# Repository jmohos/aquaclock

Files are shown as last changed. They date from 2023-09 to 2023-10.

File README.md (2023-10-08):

# AquaClock

## **What is this thing?**

The AquaClock project is a kinetic clock using water, tubes, ESP32, pumps, valves, time-of-flight sensors and Arduino to display time.

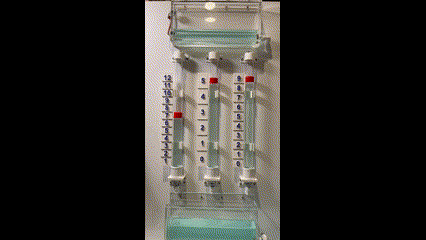
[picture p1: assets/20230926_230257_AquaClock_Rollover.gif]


## Why?

I love clocks.  The more unique the better.  One day I was touring the Queen Mary engine room and I fell in love with the steampunk style gauges.  Then inspiration hit me, why not make a clock that quietly tells time using a floating marker?

After 4 months of tinkering on Fusion360, printing 30+ 3D parts, building Arduino SW, ordering parts from Amazon, DigiKey and Pololu I have a working prototype!

## Design Goals

* Has to tell time in the form of Hours and Minutes.
* Has to be silent.  Only a slight purring of a quiet pump once an hour max.
* Has to show organic movement.
* Has to be wall hangable to install in my office.
* Has to be accurate and battery backed.
* Has to run without the need for Wifi or bluetooth.
* Has to support sleeping during specified hours.
* Has to be readable from across my office from a wide viewing angle.
* Has to have a simple user interface to set the time, set sleep periods and calibrate the markers.
* Has to manage transfering water between tanks fully automated.
* Has to be captured in a CAD program to share with others.
* Has to be fun to watch!

## 3D Design on Fusion 360

One of my personal goals was to capture the design in a 3D CAD program.  I have been playing with Fusion 360 and really enjoy using it.  So I started to pull together acrylic tubes, 1/4" tubing, fittings and colored water to experiment with gravity fed water regulation.

The result is dozens of components comprised of off the shelf parts and custom parts.  I wanted to highlight not just the water in the tubes to tell time but also the tanks holding the water for gravity feeding.  The clock needs to be kinetic, moving and organic.

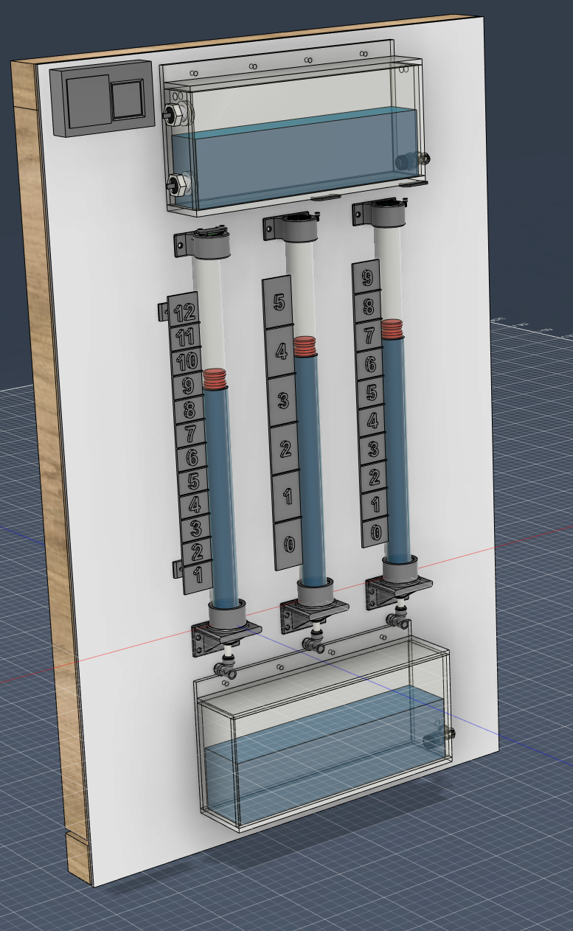
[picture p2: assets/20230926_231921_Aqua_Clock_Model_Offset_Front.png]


The back shows the array of valves, pump, plumbing and electronics to make it al work together.

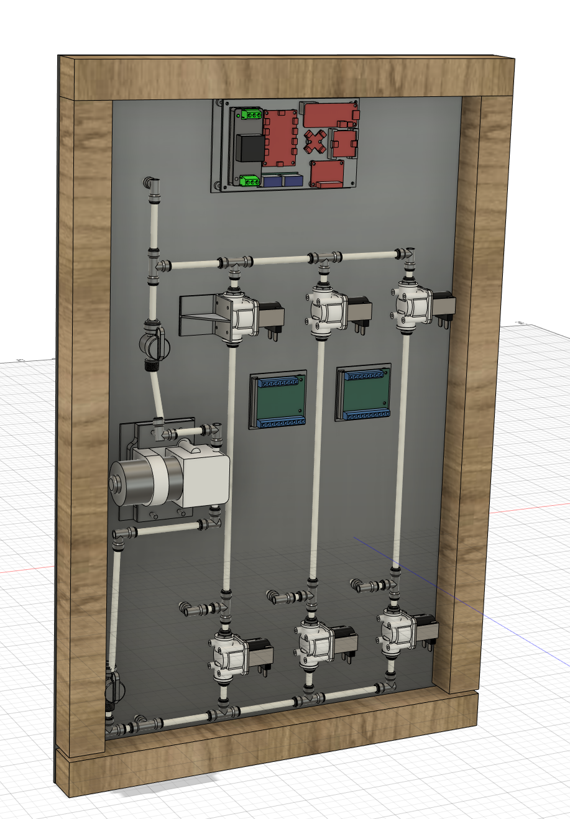
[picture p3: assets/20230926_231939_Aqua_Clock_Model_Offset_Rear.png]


## The Results

After 3D printing, fitting, glueing, sanding, painting, soldiering, criming and fastening this is the result:

Front View:



Rear View:



Here are the details highlighted:





## The Electronics
Architecture:
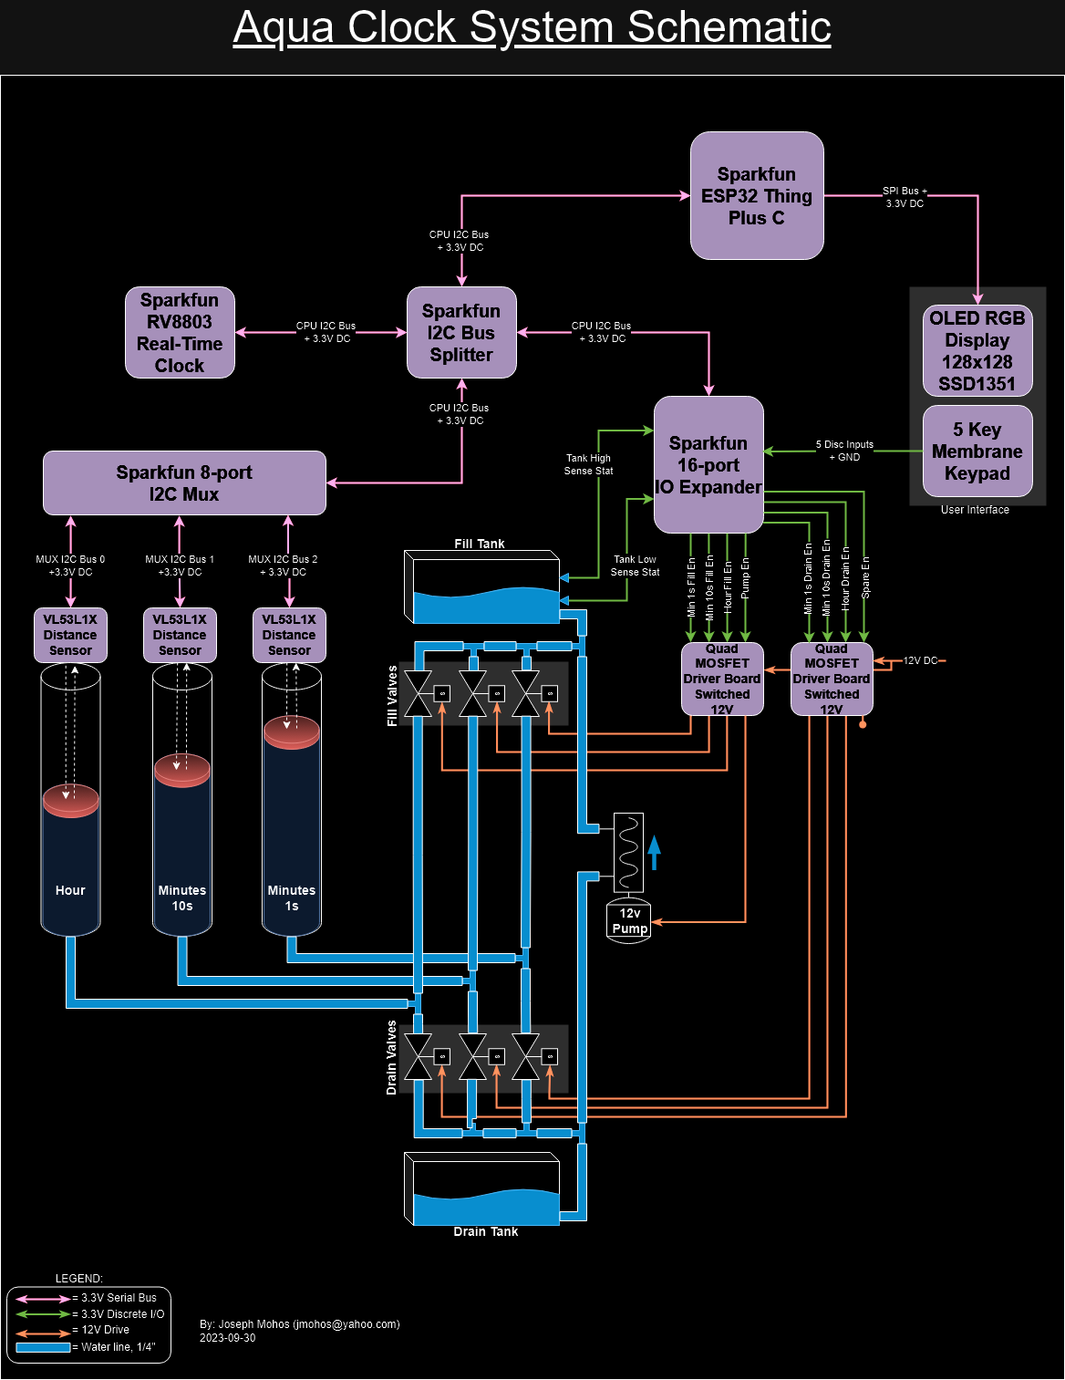
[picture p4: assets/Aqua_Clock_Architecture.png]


Schematics:
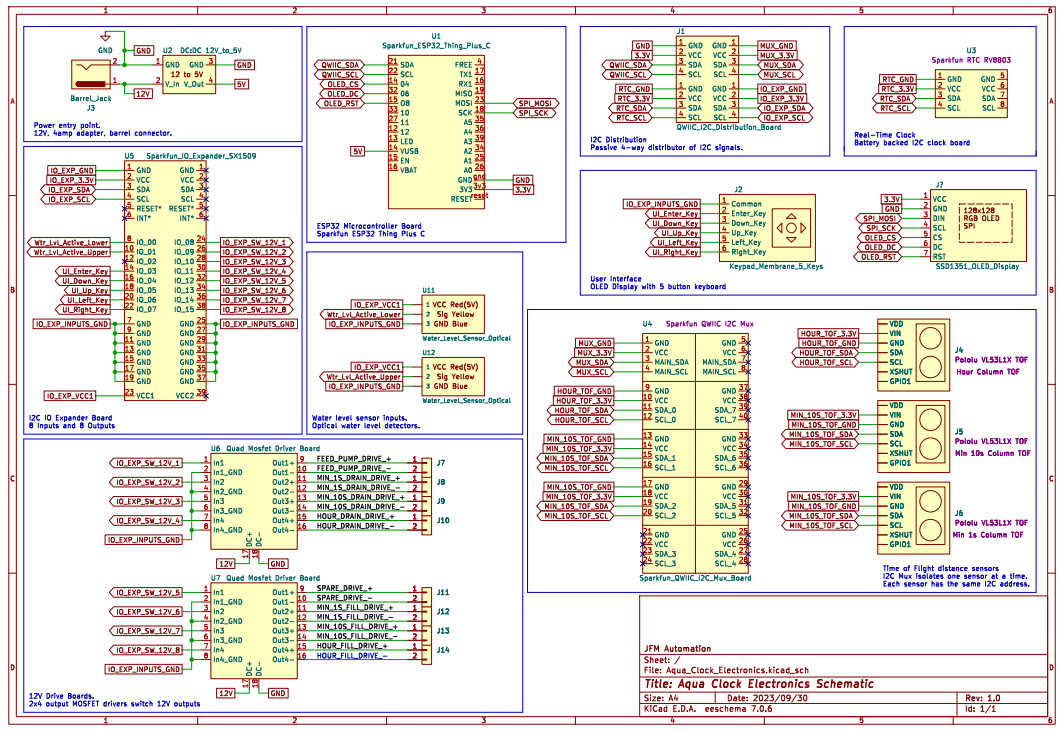
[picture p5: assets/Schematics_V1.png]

## The Software

The Sparkfun ESP32 Thing Plus C is the heart of the controls assembly.

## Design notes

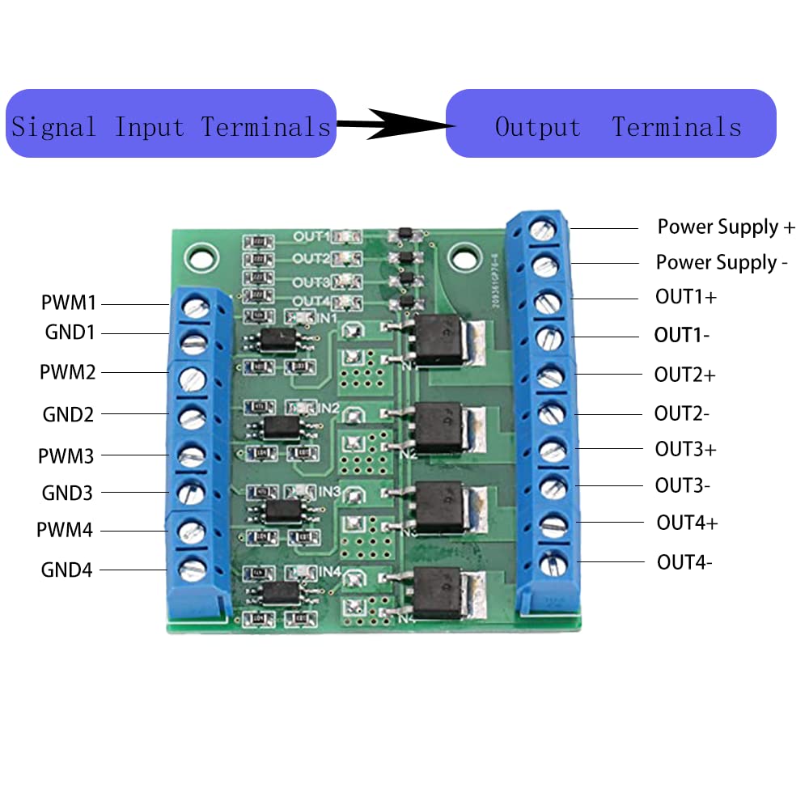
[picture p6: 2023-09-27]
parts/Quad_MOSFET_Driver_Board/Quad_Driver_Board_Pinout.jpg

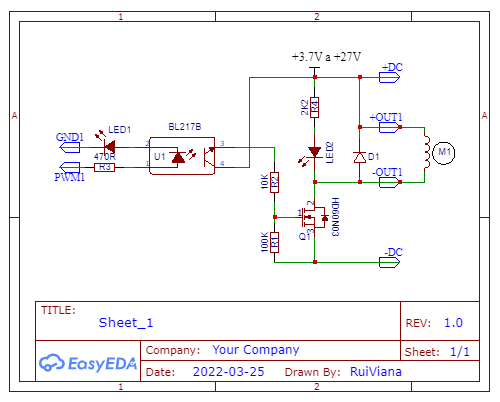
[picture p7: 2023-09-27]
parts/Quad_MOSFET_Driver_Board/Rough_Schematic.png

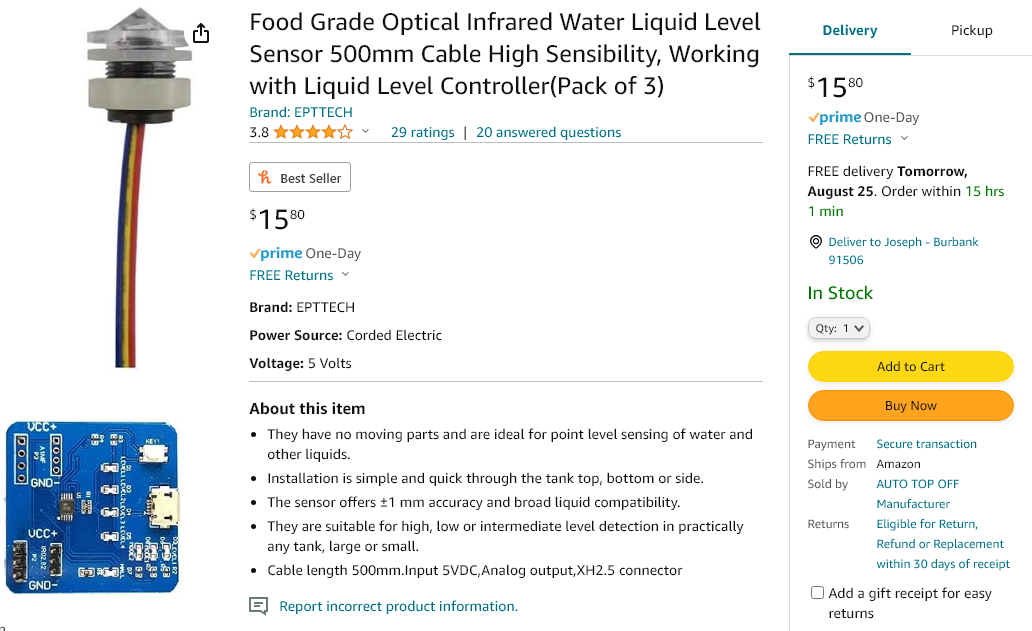
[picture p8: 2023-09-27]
parts/Water_Level_Sensor_-_Optical/Amazon_Listing.png

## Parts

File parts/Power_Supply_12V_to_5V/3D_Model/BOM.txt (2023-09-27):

3DX_CUI_Supplier: CUI, Inc
3DX_CUI_Description: 5 Vdc, 2 A, 10 W, 9~36 Vdc Input Range
3DX_CUI_Model Number: PDQE10-Q24-S5-T

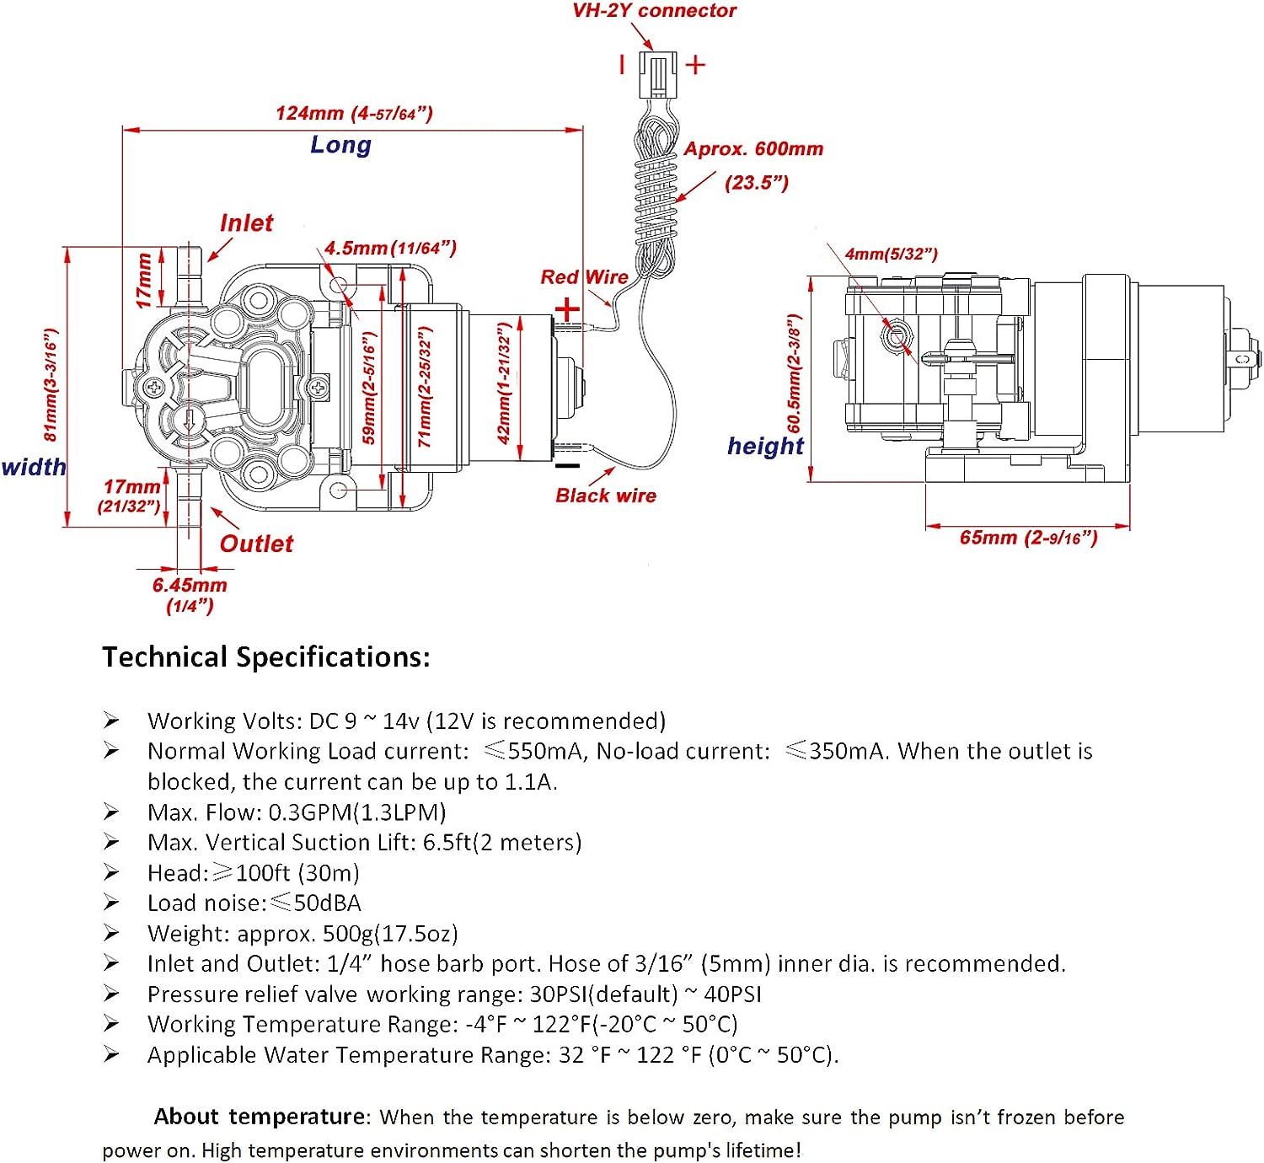
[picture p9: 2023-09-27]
parts/Water_Pump_12V/715-BqpBXsL._AC_SL1500_.jpg

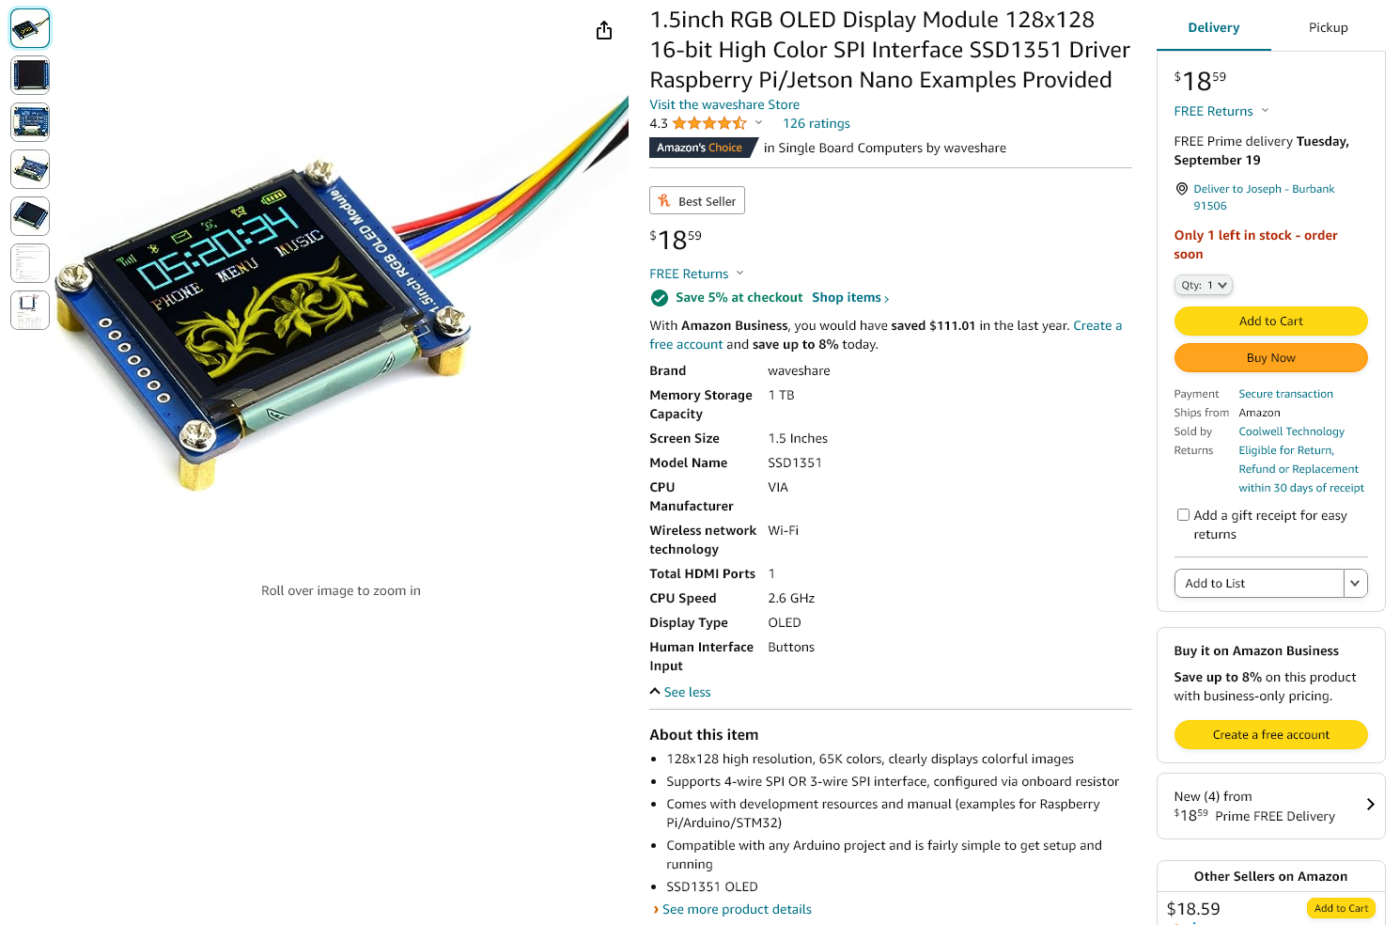
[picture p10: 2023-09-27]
parts/OLED_Display_1_5inch_Waveshare_SSD1351_128x128/Amazon_Part.png

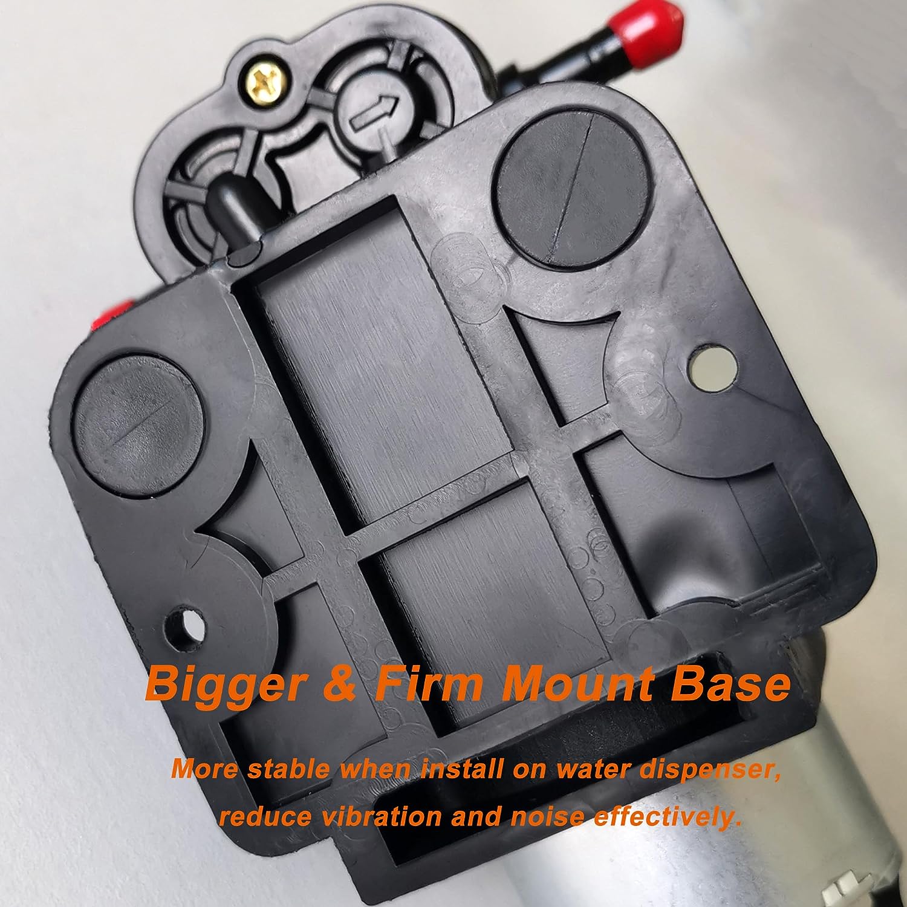
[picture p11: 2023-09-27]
parts/Water_Pump_12V/817y4+fEQSL._AC_SL1500_.jpg

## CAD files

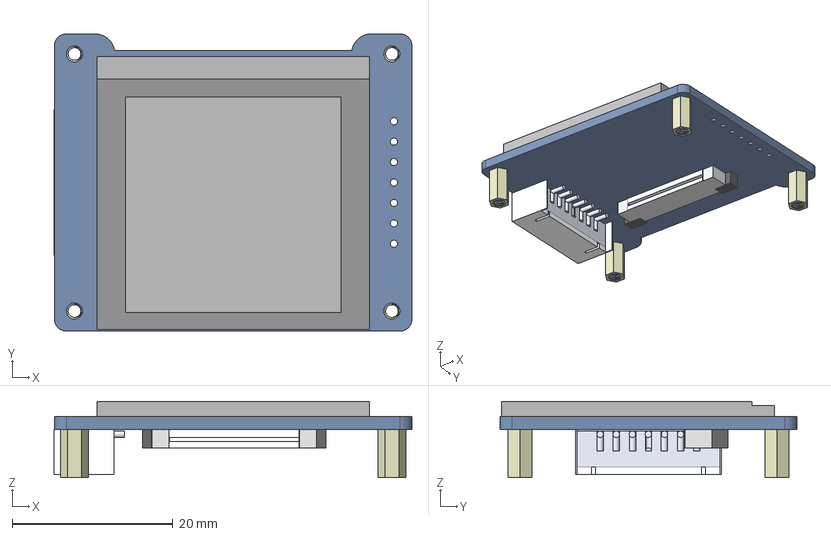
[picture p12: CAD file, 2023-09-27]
parts/OLED_Display_1_5inch_Waveshare_SSD1351_128x128/1_5inch-rgb-oled-module_asm-1110.stp
44.5 x 37.0 x 9.50 mm
1_5INCH-RGB-OLED
1_5INCH_OLED_RGB_PCBA
M2XH6_COPPER-POST x 4

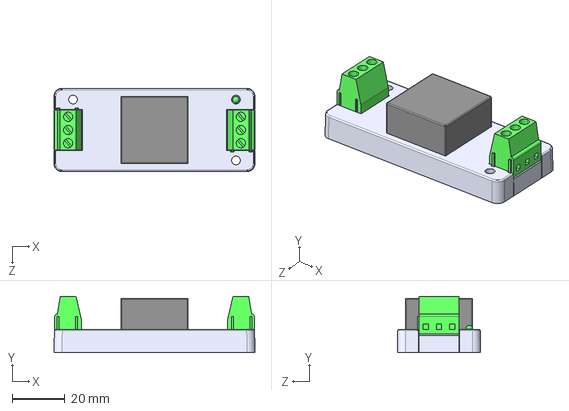
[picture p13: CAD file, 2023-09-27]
parts/Power_Supply_12V_to_5V/3D_Model/CUI_PDQE10-Q24-S5-T.step
76.0 x 21.2 x 31.5 mm
PDQE10-T base
PDQE10-D

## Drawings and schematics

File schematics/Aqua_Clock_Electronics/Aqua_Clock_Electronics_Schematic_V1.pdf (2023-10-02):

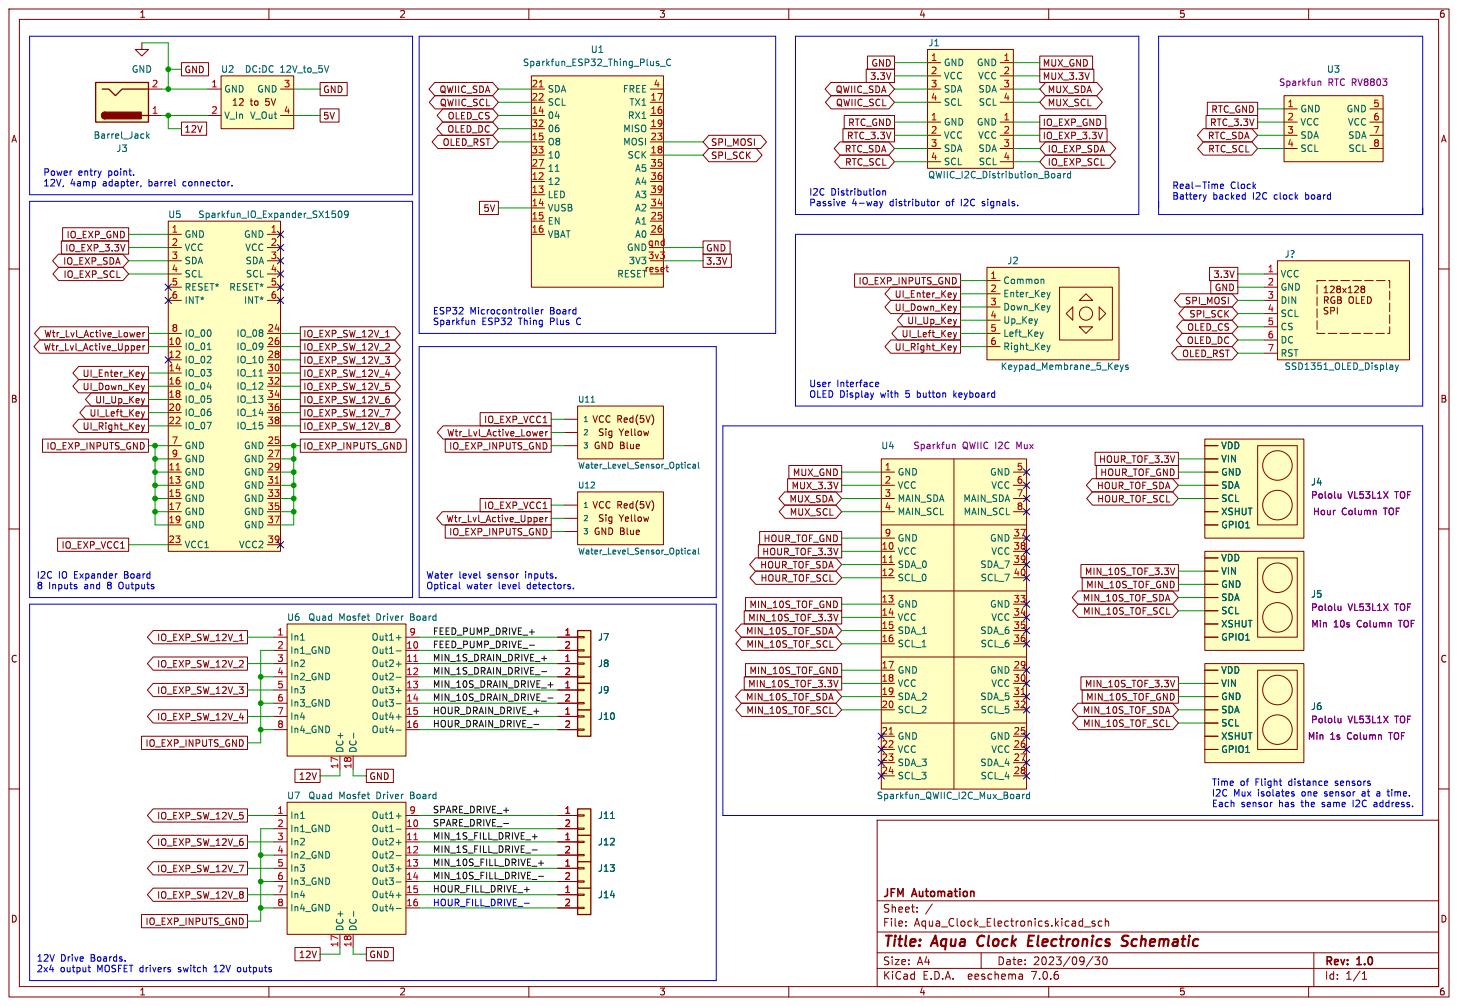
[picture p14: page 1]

J1QWIIC_I2C_Distribution_Board GND Blue Sig Yellow

J?SSD1351_OLED_Display
SPI VCC 1 GND 2 DIN 3 SCL 4 CS 5 DC 6 RST 7

VDD
VIN
J4Pololu VL53L1X TOF Hour Column TOF GND GPIO1 SCL SDA

J5Pololu VL53L1X TOF Min 10s Column TOF GND GPIO1 SCL SDA

J5Pololu VL53L1X TOF Min 10s Column TOF

J6Pololu VL53L1X TOF Min 1s Column TOF GND GPIO1 SCL SDA

J6Pololu VL53L1X TOF Min 1s Column TOF

Id: 1/1 Title: Aqua Clock Electronics Schematic

12V Drive Boards. 2x4 output MOSFET drivers switch 12V outputs

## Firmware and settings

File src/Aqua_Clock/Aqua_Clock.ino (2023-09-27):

/*
 * Joe Mohos' Aqua Clock Water Clock Project
 *
 * Date: June 2023
 * Board: Sparkfun ESP32 Thing Plus C
 * IDE: Arduino 2.1.0+
 *
 * Description:
 * This project is a kinetic clock that tells time using three columns of water with floating markers.
 * Left column is the Hours (1-12)
 * Middle column is the Minutes 10s digit (0-5)
 * Right column is the Minutes 1s digit (0-9)
 * 
 * Design Details:
 * A set of reservoir tanks hold water.
 * The top tank (feeder) is elevated above all the columns.
 * The bottom tank (holding) is elevated below all of the columns.
 * Gravity is used to flow the water from the feeder tank to the individual columns.
 * Gravity is used to drain the water from individual columns to the holding tank.
 * A set of 12V water solenoid valves control the added and subtracted water.
 * Each column has a single Time of Flight distance sensor to measure the column water height.
 * RangeUtil objects manage each column distance sensor.
 * Since each distance sensor uses the same I2C address, there is an IO Mux betwee the ESP32
 * and the sensors to select one device at a time.
 * ColumnManager objects manage each of the columns by controlling the valves based on the measured column elevations.
 * Each distance sensor can be calibrated for a more consistent reading of its column.  See calibration.h for static tables.
 * A 12V water pump is used to pipe from the holding tank to the feeder tank.
 * The upper tank has two water level sensors located at the 25 and 75 percent points.
 * A TankManager object manages the pump control based on the two water level sensors.
 * A battery backed I2C real-time clock (RV8803) is used as the official timekeeper.
 * A ClockManager object manages the I2C real-time clock to read and set the time.
 * The system monitors for a variety of potential failures which will stop any water flows.
 * All faults are collected into a single bit-encoded object with fault enums in faults.h.
 * All I/O is managed using an I2C IO expander (SX1509).
 * All IO expander pin definitions are captured in io_expander_config.h.
 * There are 6 12V water solenoid valves wired to a pair of 4 channel mosfet boards that switch 12V to
 * each solenoid.  The IO expander is used to output the 6 drive lines to the mosfet board.
 * For each column there is one fill and one drain valve.
 * All ESP32 microcontroller pins are mapped in pins.h.
 * For diagnostics a serial port console is created to allow for getting status and issuing commands.
 * The console runs at 115200 baud on the primary USB serial port.  Commands need to be sent with a carriage return.
 * Use the HELP command to get a list of comamnds supported.
 * A UI handler is created to manage the user interface.  The UI is a combination of a 128x128 RGB OLED display
 * and a 5 button keypad with keys for UP, DOWN, LEFT, RIGHT and SELECT.
 * The display, SSD1351, 128,128 pixel OLED display wired to the primary SPI interface of the ESP32.
 * The keypad is wired to the inputs of the IO expander.
 *
 * Arduino Project Prerequisits:
 *   ESP32 for Arduino (For Sparkfun ESP32 Thing Plus C)
 *   Preferences library for ESP32, for EEPROM save/restore.
 *   VL53L1X library for Arduino by Pololu
 *   Sparkfun Qwiic I2C Mux Arduino Library
 *   Sparkfun Qwiic RTC RV8803 Arduino Library
 *   Sparkfun SX1509 IO Expander
 *   LED Display Support
 *     Adafruit GFX library (V1.11.7+)
 *     Adafruit SSD1351
 *   elapsedMillis
 *   InterpolationLib by Luis Llamas.  (Must use V1.0.1 or greater for ESP32! See libs folder)
 *
 * @author Joe Mohos
 * Contact: jmohos@yahoo.com
*/
#include <Arduino.h>
#include <InterpolationLib.h>
#include <Preferences.h>
#include <Wire.h>

#include <SparkFun_I2C_Mux_Arduino_Library.h>  //Click here to get the library: http://librarymanager/All#SparkFun_I2C_Mux
#include <VL53L1X.h>                           /* Pololu VL32L1X Library */
#include "calibration.h"
#include "faults.h"
#include "io_expander_config.h"
#include "ClockManager.h"
#include "ColumnManager.h"
#include "Console.h"
#include "RangeUtil.h"
#include "TankManager.h"
#include "UIManager.h"



//
// I2C Devices
//
QWIICMUX i2c_mux;   /* Used to access multiple ToF sensors with same I2C address */
SX1509 io_expander; /* Discrete I/O interface */
VL53L1X range_sensor_hour_column;
VL53L1X range_sensor_min_10s_column;
VL53L1X range_sensor_min_1s_column;
RangeUtil range_util_hour_column(&range_sensor_hour_column, 1);        // Sensor #1
RangeUtil range_util_min_10s_column(&range_sensor_min_10s_column, 2);  // Sensor #2
RangeUtil range_util_min_1s_column(&range_sensor_min_1s_column, 3);    // Sensor #3


//
// Console handler
//
Console console;

//
// User interface handler
//
UIManager *ui_manager;

//
// Tank and water column handlers
//
TankManager *tank_manager;
ColumnManager *column_manager_hour;
ColumnManager *column_manager_min_10s;
ColumnManager *column_manager_min_1s;

const uint16_t MIN_WATER_COLUMN_ELEVATION = 50;
const uint16_t MAX_WATER_COLUMN_ELEVATION = 305;

//
// Define time management elements.
//
ClockManager clock_manager;

// Status streamer
bool stream_status = false;
elapsedMillis stream_status_elapsed;
static constexpr int STREAM_STATUS_PERIOD_MS = 250;

// Heartbeat LED
elapsedMillis heartbeat_elapsed;
static constexpr int HEARTBEAT_LED_PERIOD_MS = 500;

// Bit encoded system fault status and string representations.  See faults.h for bit defintions.
uint32_t system_faults = 0;
const char *FAULT_STRING[] = {
  "I2C_MUX_OFFLINE",
  "I2C_MUX_PORT_0_FAIL",
  "I2C_MUX_PORT_1_FAIL",
  "I2C_MUX_PORT_2_FAIL",
  "VL53L1X_SENSOR_1_INIT_FAIL",
  "VL53L1X_SENSOR_2_INIT_FAIL",
  "VL53L1X_SENSOR_3_INIT_FAIL",
  "VL53L1X_UNKNOWN_INIT_FAIL",
  "L53L1X_SENSOR_1_TIMEOUT",
  "VL53L1X_SENSOR_2_TIMEOUT",
  "VL53L1X_SENSOR_3_TIMEOUT",
  "VL53L1X_UNKNOWN_TIMEOUT",
  "RV8803_RTC_INIT_FAIL",
  "RV8803_RTC_READ_FAULT",
  "RV8803_RTC_SET_TIME_FAULT",
  "SX1509_IO_EXPANDER_INIT_FAIL",
  "TANK_FILL_TIMEOUT",
  "TANK_LEVEL_SENSE_FAIL",
  "NVM_FAIL"
};



//
// Master project setup entry.  Called once right after powerup.
//
void setup() {
  //
  // CPU diagnostic light setup
  //
  pinMode(LED_BUILTIN, OUTPUT);
  digitalWrite(LED_BUILTIN, HIGH);

  //
  // Serial Port Config
  //
  Serial.begin(115200);
  Serial.println("Bootup of the AquaClock...");

  //
  // I2C bus initialization.  Used for RTC, IO Expander, Mux, Range Sensors, etc.
  //
  Wire.begin();
  Wire.setClock(400000);


  //
  // Real-time clock initialization.  Used to maintain time in battery backed clock outside of CPU.
  //
  clock_manager.Startup();

  //
  // Initialize the command console via the main serial port for diagnostics, calibration, status checks, etc.
  //
  console.Setup(&Serial);
  console.SetConsoleRxCallback(&console_rx_event);

  //
  // I2C IO Expander initialization.  SX1509 chip used for 8 inputs and 8 outputs.
  //
  if (io_expander.begin(SX1509_ADDRESS) == false) {
    // We faild to find the IO expander
    FAULT_SET(FAULT_SX1509_IO_EXPANDER_INIT_FAIL);
    Serial.println("ERROR: Failed to start SX1509 IO Expander!");
  } else {
    // Configure the IO expander input bank (pins 0-7)
    for (int i = 0; i < 8; i++) {
      io_expander.pinMode(i, INPUT_PULLUP);
    }

    // Configure the IO expander output bank (pins 8-15)
    for (int i = 8; i < 16; i++) {
      io_expander.pinMode(i, OUTPUT);
    }
  }

  //
  // I2C Mux initialization.  Used to access a multitude of I2C sensors with the same address.
  //
  if (i2c_mux.begin() == false) {
    FAULT_SET(FAULT_I2C_MUX_OFFLINE);
    Serial.println("ERROR: I2C Mux not detected!");
  }

  //
  // I2C ranging device initialization. Time-of-flight sensors to measure distance in each column.
  // Each range sensor uses the same I2C address so a mux is needed to limit coms with only one
  // sensor at a time.  Hour sensor is on mux port 0, etc.
  //
  if (!FAULT_ACTIVE(FAULT_I2C_MUX_OFFLINE)) {
    if (i2c_mux.setPort(0) == false) {
      // Hour mux port failed
      FAULT_SET(FAULT_I2C_MUX_PORT_0_FAIL);
    } else {
      // Initialize the Hour column range sensor on i2c mux port 0
      range_util_hour_column.Startup();
    }
    if (i2c_mux.setPort(1) == false) {
      // Minutes 10s mux port failed
      FAULT_SET(FAULT_I2C_MUX_PORT_1_FAIL);
    } else {
      // Initialize the Minute 10s column range sensor on i2c mux port 1
      range_util_min_10s_column.Startup();
    }
    if (i2c_mux.setPort(2) == false) {
      // Minutes 1s mux port failed
      FAULT_SET(FAULT_I2C_MUX_PORT_2_FAIL);
    } else {
      // Initialize the Minute 1s column range sensor on i2c mux port 2
      range_util_min_1s_column.Startup();
    }
  } else {
    Serial.print("Skipping range sensor inits due to missing I2C Mux...");
  }

  //
  // Create and configure the tank manager and column handlers
  // These objects regulate the functions of the tank refill pump and the column fill and drain valves.
  //
  tank_manager = new TankManager(&io_expander,
                                 SC1509_PIN_FEED_PUMP,
                                 SX1509_PIN_WATER_LOW,
                                 SC1509_PIN_WATER_HIGH);
  column_manager_hour = new ColumnManager(1,
                                          &io_expander,
                                          SC1509_PIN_HOUR_FEED,
                                          SC1509_PIN_HOUR_DRAIN,
                                          MIN_WATER_COLUMN_ELEVATION,
                                          MAX_WATER_COLUMN_ELEVATION);
  column_manager_min_10s = new ColumnManager(2,
                                             &io_expander,
                                             SC1509_PIN_MIN_10s_FEED,
                                             SC1509_PIN_MIN_10s_DRAIN,
                                             MIN_WATER_COLUMN_ELEVATION,
                                             MAX_WATER_COLUMN_ELEVATION);
  column_manager_min_1s = new ColumnManager(3,
                                            &io_expander,
                                            SC1509_PIN_MIN_1s_FEED,
                                            SC1509_PIN_MIN_1s_DRAIN,
                                            MIN_WATER_COLUMN_ELEVATION,
                                            MAX_WATER_COLUMN_ELEVATION);


  //
  // Create and start the UI handler
  // It needs access to the sensors, regulators and clock.
  //
  ui_manager = new UIManager(&io_expander,
                             &range_util_hour_column,
                             &range_util_min_10s_column,
                             &range_util_min_1s_column,
                             column_manager_hour,
                             column_manager_min_10s,
                             column_manager_min_1s,
                             tank_manager,
                             &clock_manager);
  ui_manager->Startup();

  //
  // Activate clock mode as the default
  //
  ui_manager->Set_Operating_Mode(UIManager::OPERATING_MODE_CLOCK);
}


//
// After setup this function is repeatedly called at the fastest rate possible by the processor.
// Rate control must be done in each component being updated.
//
void loop() {

  //
  // Run the console interface and process commands
  //
  console.Loop();

  //
  // Real-Time Clock read
  //
  clock_manager.Update();

  // Process the user interface menu
  ui_manager->Update();


  //
  // Compute the desired float marker elevations for the Hour, Min_10s and Min_1s columns.
  // This is done by taking the time and splitting it into the relevant digits and scaling
  // to a range sensor target.
  // There are provisions to override the target setpoint in the console for tuning purposes.
  //
  uint16_t hour_setpoint;
  if (ui_manager->Get_Hour_Column_Override_Setpoint_Enable()) {
    // User the diagnostic override value for the hour column setpoint
    hour_setpoint = ui_manager->Get_Hour_Column_Override_Setpoint();
  } else if (clock_manager.Is_Sleep_Time()) {
    // Use the sleep mode setpoint for the hour column setpoint
    hour_setpoint = 300;
  } else {
    // Use the scaled clock time to drive the hour column setpoint
    hour_setpoint = scale_hours_to_elevation(clock_manager.Get_Hour());
  }

  uint16_t min_10s_setpoint;
  if (ui_manager->Get_Min_10s_Column_Override_Setpoint_Enable()) {
    // User the diagnostic override value for the min 10s column setpoint
    min_10s_setpoint = ui_manager->Get_Min_10s_Column_Override_Setpoint();
  } else if (clock_manager.Is_Sleep_Time()) {
    // Use the sleep mode setpoint for the min 10s column setpoint
    min_10s_setpoint = 300;
  } else {
    // Use the scaled clock time to drive the min 10s column setpoint
    min_10s_setpoint = scale_minutes_10s_to_elevation(clock_manager.Get_Minute());
  }

  uint16_t min_1s_setpoint;
  if (ui_manager->Get_Min_1s_Column_Override_Setpoint_Enable()) {
    // User the diagnostic override value for the min 1s column setpoint
    min_1s_setpoint = ui_manager->Get_Min_1s_Column_Override_Setpoint();
  } else if (clock_manager.Is_Sleep_Time()) {
    // Use the sleep mode setpoint for the min 1s column setpoint
    min_1s_setpoint = 300;
  } else {
    // Use the scaled clock time to drive the min 1s column setpoint
    min_1s_setpoint = scale_minutes_1s_to_elevation(clock_manager.Get_Minute());
  }

  //
  // Update sensor readings and linearize with calibration table
  //
  i2c_mux.setPort(0);
  range_util_hour_column.Update();
  // Linearize this column raw reading
  double raw_median_range = (double)range_util_hour_column.Get_Median_Reading();
  double linearized_range = Interpolation::Linear(hour_range_cal_x_values,
                                                  hour_range_cal_y_values,
                                                  NUM_RANGE_CAL_BREAKS,
                                                  raw_median_range,
                                                  true);
  range_util_hour_column.Set_Linearized_Median_Reading((uint16_t)linearized_range);
  //Serial.print("  LINEARIZE ");
  //Serial.print(raw_median_range);
  //Serial.print(" to ");
  //Serial.println(linearized_range);

  i2c_mux.setPort(1);
  range_util_min_10s_column.Update();
  // Linearize this column raw reading
  raw_median_range = (double)range_util_min_10s_column.Get_Median_Reading();
  linearized_range = Interpolation::Linear(min_10s_range_cal_x_values,
                                           min_10s_range_cal_y_values,
                                           NUM_RANGE_CAL_BREAKS,
                                           raw_median_range,
                                           true);
  range_util_min_10s_column.Set_Linearized_Median_Reading((uint16_t)linearized_range);
  //Serial.print("  LINEARIZE ");
  //Serial.print(raw_median_range);
  //Serial.print(" to ");
  //Serial.println(linearized_range);

  i2c_mux.setPort(2);
  range_util_min_1s_column.Update();
  // Linearize this column raw reading
  raw_median_range = (double)range_util_min_1s_column.Get_Median_Reading();
  linearized_range = Interpolation::Linear(min_1s_range_cal_x_values,
                                           min_1s_range_cal_y_values,
                                           NUM_RANGE_CAL_BREAKS,
                                           raw_median_range,
                                           true);
  range_util_min_1s_column.Set_Linearized_Median_Reading((uint16_t)linearized_range);
  //Serial.print("  LINEARIZE ");
  //Serial.print(raw_median_range);
  //Serial.print(" to ");
  //Serial.println(linearized_range);

  //
  // Process each water column regulator with the latest column elevation, setpoint and override requests.
  // Support overrides for turning the drain and fill valves on for maintenance.
  //
  bool busy = column_manager_hour->Update(range_util_hour_column.Get_Linearized_Median_Reading(),
                                          hour_setpoint);

  busy |= column_manager_min_10s->Update(range_util_min_10s_column.Get_Linearized_Median_Reading(),
                                         min_10s_setpoint);

  busy |= column_manager_min_1s->Update(range_util_min_1s_column.Get_Linearized_Median_Reading(),
                                        min_1s_setpoint);

  // Process the tank_manager manager
  //if (!busy)
  //{
  tank_manager->Update();
  //}


  //
  // Stream a status line to the console for tuning if enabled in the console.
  //
  if (stream_status) {
    if (stream_status_elapsed >= STREAM_STATUS_PERIOD_MS) {
      stream_status_elapsed = 0;
      report_status_stream();
    }
  }


  //
  // React to system faults
  //
  if (system_faults != 0x0000) {
    // Disable the regulators to prevent water/pump actuation with bad sensor inputs
    tank_manager->Set_Regulator_Enable(false);
    column_manager_hour->Set_Regulator_Enable(false);
    column_manager_min_10s->Set_Regulator_Enable(false);
    column_manager_min_1s->Set_Regulator_Enable(false);
  }


  //
  // Toggle hearthbeat/fault status LED
  // Blink out a status, either healthy or a fault code in case a major component failure is detected.
  //
  if (heartbeat_elapsed >= HEARTBEAT_LED_PERIOD_MS) {
    heartbeat_elapsed = 0;
    digitalWrite(LED_BUILTIN, !digitalRead(LED_BUILTIN));
  }
  //TODO: Add fault blink pattern generator
}


//
//
//
uint16_t scale_hours_to_elevation(uint16_t hours) {
  if (hours > 12) {
    hours = hours - 12;
  }

  // Scale 1-12 hours into hour_col_digit_elevations[NUM_HOUR_STEPS]
  if ((hours >= 1) && (hours <= 12)) {
    uint16_t elevation = hour_col_digit_elevations[hours - 1];
    return elevation;
  } else {
    // Invalid time, set to safe value
    return 150;
  }
}


//
//
//
uint16_t scale_minutes_10s_to_elevation(uint16_t minutes) {
  // Scale minutes 10s 0-5 into min_10s_col_digit_elevations[NUM_MIN_10S_STEPS]
  if ((minutes >= 0) && (minutes <= 59)) {
    uint16_t min_10s = minutes / 10;
    uint16_t elevation = min_10s_col_digit_elevations[min_10s];
    return elevation;
  } else {
    // Invalid time, set to safe value
    return 150;
  }
}

//
//
//
uint16_t scale_minutes_1s_to_elevation(uint16_t minutes) {
  // Scale minutes 1s 0-9 into elevation steps in min_1s_col_digit_elevations[NUM_MIN_1S_STEPS]
  if ((minutes >= 0) && (minutes <= 59)) {
    uint16_t min_1s = minutes - ((minutes / 10) * 10);
    uint16_t elevation = min_1s_col_digit_elevations[min_1s];
    return elevation;
  } else {
    // Invalid time, set to safe value
    return 150;
  }
}


//
//
//
void print_tank_state(TankManager *tank_manager) {
  TankManager::TANK_STATE_TYPE_T state = tank_manager->Get_State();
  switch (state) {
    case TankManager::TANK_IDLE:
      Serial.print("IDLE");
      break;

    case TankManager::TANK_FILL_ACTIVE:
      Serial.print("FILL_ACTIVE");
      break;

    case TankManager::TANK_FILL_SETTLE:
      Serial.print("FILL_SETTLE");
      break;

    case TankManager::TANK_MANUAL_FILL:
      Serial.print("MANUAL_FILL");
      break;

    case TankManager::TANK_FILL_TIMEOUT_FAULT:
      Serial.print("TANK_FILL_TIMEOUT");
      break;

    default:
      Serial.print("UNKNOWN");
      break;
  }
}




//
//
//
void print_column_state(ColumnManager *column) {
  ColumnManager::COLUMN_STATE_TYPE_T state = column->Get_State();
  switch (state) {
    case ColumnManager::COLUMN_IDLE:
      Serial.print("IDLE");
      break;

    case ColumnManager::COLUMN_DRAIN_ACTIVE:
      Serial.print("DRAIN_ACTIVE");
      break;

    case ColumnManager::COLUMN_DRAIN_SETTLE:
      Serial.print("DRAIN_SETTLE");
      break;

    case ColumnManager::COLUMN_FILL_ACTIVE:
      Serial.print("FILL_ACTIVE");
      break;

    case ColumnManager::COLUMN_FILL_SETTLE:
      Serial.print("FILL_SETTLE");
      break;

    case ColumnManager::COLUMN_MANUAL_DRAIN:
      Serial.print("MANUAL_DRAIN");
      break;

    case ColumnManager::COLUMN_MANUAL_FILL:
      Serial.print("MANUAL_FILL");
      break;

    case ColumnManager::COLUMN_ERROR_STATE:
      Serial.print("COLUMN_ERROR");
      break;

    default:
      Serial.print("UNKNOWN");
      break;
  }
}


//
//
//
void print_column_control_error_state(ColumnManager *column) {
  ColumnManager::CONTROL_ERROR_STATE_TYPE_T control_error_state = column->Get_Control_Error_State();
  switch (control_error_state) {
    case ColumnManager::CONTROL_ERROR_DEADBAND:
      Serial.print("IN_DEADBAND");
      break;
    case ColumnManager::CONTROL_ERROR_POSITIVE:
      Serial.print("POSITIVE");
      break;
    case ColumnManager::CONTROL_ERROR_NEGATIVE:
      Serial.print("NEGATIVE");
      break;
    default:
      Serial.print("UNKNOWN");
      break;
  }
}


//
//
//
void print_active_faults() {
  for (int i = 0; i < FAULT_MAX_INDEX; i++) {
    if (FAULT_ACTIVE(i)) {
      Serial.println(FAULT_STRING[i]);
    }
  }
}
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

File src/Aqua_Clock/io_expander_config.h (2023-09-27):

/*
 * IO Expander pin definitions
 *
 * A Sparkfun SX1509 IO expander board is connected to the ESP32 va I2C.
 * The expander board has 16 totals pins, configured for 8 inputs and 8 outputs.
 * The pin mappings are defined in this file.
 *
 * @author Joe Mohos
 * Contact: jmohos@yahoo.com
 */
#ifndef IO_EXPANDER_CONFIG_H
#define IO_EXPANDER_CONFIG_H


#include <Wire.h>            // Include the I2C library (required)
#include <SparkFunSX1509.h>  //Click here for the library: http://librarymanager/All#SparkFun_SX1509

// SX1509 I2C address (set by ADDR1 and ADDR0 (00 by default):
#define SX1509_ADDRESS 0x3E

// Pin Definitions Inputs
#define SX1509_PIN_WATER_LOW 0
#define SC1509_PIN_WATER_HIGH 1
#define SC1509_PIN_KEY_1 3
#define SC1509_PIN_KEY_2 4
#define SC1509_PIN_KEY_3 5
#define SC1509_PIN_KEY_4 6
#define SC1509_PIN_KEY_5 7


// Pin Definitions Outputs
#define SC1509_PIN_FEED_PUMP 8
#define SC1509_PIN_FEED_VALVE 12
#define SC1509_PIN_HOUR_FEED 15
#define SC1509_PIN_HOUR_DRAIN 11
#define SC1509_PIN_MIN_10s_FEED 14
#define SC1509_PIN_MIN_10s_DRAIN 10
#define SC1509_PIN_MIN_1s_FEED 13
#define SC1509_PIN_MIN_1s_DRAIN 9

#endif

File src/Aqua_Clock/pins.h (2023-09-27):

/*
 * Pin definitions for the ESP32 microcontroller.
 * These are only for the ESP32 native pins.
 * See the io_expander_config.h for the IO expander pin definitions.
 *
 * @author Joe Mohos
 * Contact: jmohos@yahoo.com
 */
#ifndef PINS_H
#define PINS_H

// SPI pins used for the OLED display
#define SPI_OLED_MOSI_PIN 23
#define SPI_OLED_CLK_PIN 18
#define SPI_OLED_CS_PIN 14
#define SPI_OLED_DC_PIN 32
#define SPI_OLED_RST_PIN 15

#endif

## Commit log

2023-09-27 Upload base SW, photos and parts
    [1_5inch-rgb-oled-module_asm-1110.stp, CUI_PDQE10-Q24-S5-T.step]
2023-10-01 Update UIManager.h
    Fix bug in ui. Date edit screen month increment used minutes field in error.
    [UIManager.h]
2023-10-02 Schematics upload
    Added the schematics initial load along with a PDF export of V1.
    [Aqua_Clock_Electronics.kicad_pcb, Aqua_Clock_Electronics.kicad_sch]
2023-10-02 Upload Kicad library of custom parts.
